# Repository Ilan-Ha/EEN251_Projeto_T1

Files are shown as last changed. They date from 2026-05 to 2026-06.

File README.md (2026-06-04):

# Bebedouro Inteligente para Pets

## Integrantes do Grupo:
- Diego Mourão Oliveira
- Ilan Hameiry
- Luca Lopes Martinho

## Descrição do Projeto

O projeto consiste no desenvolvimento de um dispositivo IoT voltado para o fornecimento de água corrente para animais de estimação (pets), com foco em uso residencial.

O objetivo principal é oferecer uma forma mais atrente e confortável de hidratação para o animal, simulando o fluxo de água corrente, além de monitorar a frequência com que o pet utiliza o bebedouro.

O sistema será ativado automaticamente apenas quando houver presença do animal próxima ao dispositivo, evitando desperdício de energia e água.

## Funcionamento do Sistema

O bebedouro funcionará em ciclo contínuo de circulação de água entre a bomba e o reservatório, simulando água corrente.

Por meio de um sensor de presença por distância (ultrassônico), o sistema será ativado automaticamente quando o animal se aproximar.

Após a detecção, o dispositivo permanecerá ligado por alguns segundos mesmo após a ausência de presença, garantindo tempo suficiente para o pet se hidratar.

Além disso, o sistema contará com:

- Iluminação interna por LEDs, acionada automaticamente quando a luminosidade do ambiente estiver baixa;
- Display informativo com dados importantes de uso;
- Monitoramento do nível de água no reservatório;
- Alertas de nível baixo de água;
- Botão de ativação manual;
- Botão de reset do sistema;
- Envio de notificações e informações para um software externo via Bluetooth.

## Objetivos do Projeto

- Melhorar a experiência de hidrtação dos pets;
- Automatizar o fornecimento de água;
- Reduzir desperdícios de energia e água;
- Permitir o monitoramento do uso do bebedouro;
- Fornecer alertas e informações em tempo real ao usuário.

## Requisitos do Sistema

### Requisitos Obrigatórios

| ID | Requisito | Tipo |
|---|---|---|
| RO-01 | Água circulando entre bomba e funil | Obrigatório |
| RO-02 | Detector de presença por distância (sensor ultrassônico) | Obrigatório |
| RO-03 | Iluminação em LED quando necessário | Obrigatório |
| RO-04 | Botão para ativação manual | Obrigatório |
| RO-05 | Botão de reset | Obrigatório |

### Requisitos Desejáveis

| ID | Requisito | Tipo |
|---|---|---|
| RD-01 | Display com informações úteis de uso: nível de água e número de ativações | Desejável |
| RD-02 | Mensagem via Bluetooth quando houver presença detectada ou nível baixo de água | Desejável |
| RD-03 | Sensor de nível de água | Desejável |

### Requisitos Opcionais

| ID | Requisito | Tipo |
|---|---|---|
| ROP-03 | Programação de ativação em intervalos de tempo definidos | Opcional |

## Diagrama de Blocos
```mermaid
flowchart TD
    MCU["Microcontrolador<br/>(Raspberry Pi Pico)"]

    OLED["Display<br/>OLED I2C<br/>128x32 Px"]
    RTC["Módulo Real Time Clock<br/>DS1307 (Opcional)"]
    LDR["Sensor de Luz<br/>LDR"]
    SOIL["Sensor de nível<br/>de água"]
    BT["Módulo Bluetooth<br/>HM10"]

    LEVEL1["Conversor de Nível Lógico<br/>(5V ↔ 3.3V)"]
    US["Sensor de Distância<br/>Ultrassom HC-SR04"]

    LEVEL2["Conversor de Nível Lógico<br/>(5V ↔ 3.3V)"]
    RELAY["Módulo Relé"]
    PUMP["Mini Bomba de Água<br/>DC-JT160"]

    MCU --> OLED 
    RTC --> MCU
    LDR --> MCU
    SOIL --> MCU
    MCU --> BT

    US --> LEVEL1
    LEVEL1 --> MCU

    MCU --> LEVEL2
    LEVEL2 --> RELAY
    RELAY --> PUMP

    %% Optional styling
    classDef sensor fill:#cfe8f3,stroke:#333,stroke-width:1px;
    classDef converter fill:#f4c542,stroke:#333,stroke-width:1px;
    classDef relay fill:#6abf4b,stroke:#333,stroke-width:1px;
    classDef controller fill:#cfe8f3,stroke:#333,stroke-width:2px;

    class MCU controller;
    class OLED,RTC,LDR,SOIL,BT,US,PUMP sensor;
    class LEVEL1,LEVEL2 converter;
    class RELAY relay;
    classDef default fill:#cfe8f3,color:#000,stroke:#000,stroke-width:2px;

    linkStyle default stroke:#000,stroke-width:2px;
```

## Softwares Utilizados

Durante o desenvolvimento do projeto foram utilizados os seguintes softwares:

- KiCad — utilizado para esquematização eletrônica e desenvolvimento do diagrama/layout da PCB;
- Thonny — utilizado para programação, testes e depuração do Raspberry Pi Pico;
- Autodesk Fusion 360, Solidworks — utilizados para modelagem 3D da estrutura do bebedouro;

## Tecnologias Envolvidas

O projeto utiliza conceitos de:

- Internet das Coisas (IoT)
- Sensores ultrassônicos
- Sensores de nível de água
- Iluminação automatizada com LEDs
- Comunicação via Bluetooth
- Sistemas embarcados
- Automação residencial

## Imagens do Modelo

| Vista Frontal | Vista Lateral |
| :---: | :---: |
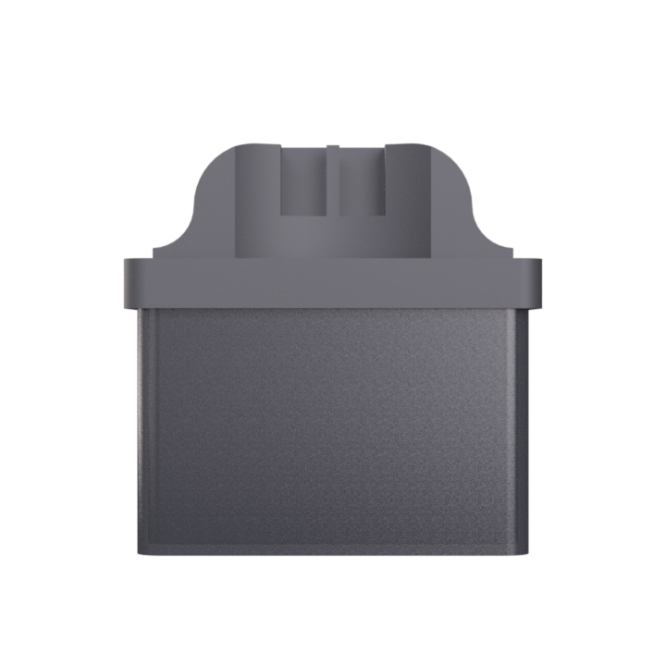
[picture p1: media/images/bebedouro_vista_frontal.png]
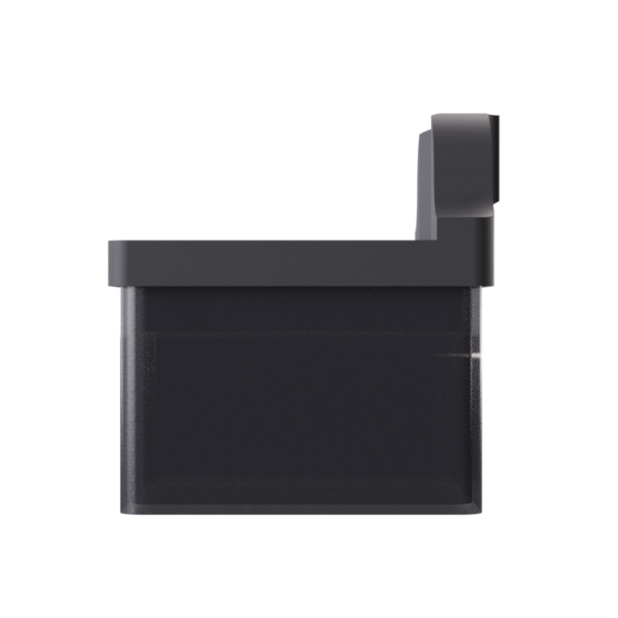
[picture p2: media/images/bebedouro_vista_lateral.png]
|  |  |
| Vista Superior | Vista Isométrica |
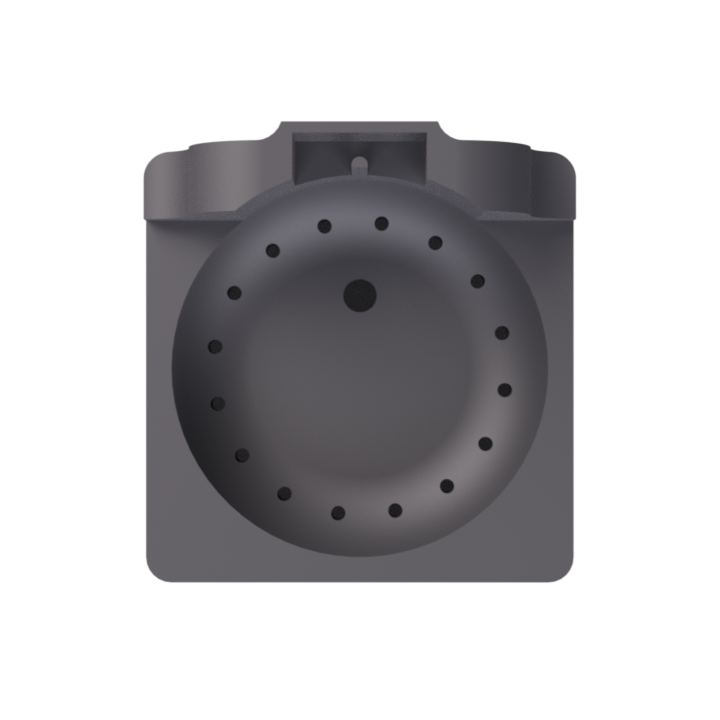
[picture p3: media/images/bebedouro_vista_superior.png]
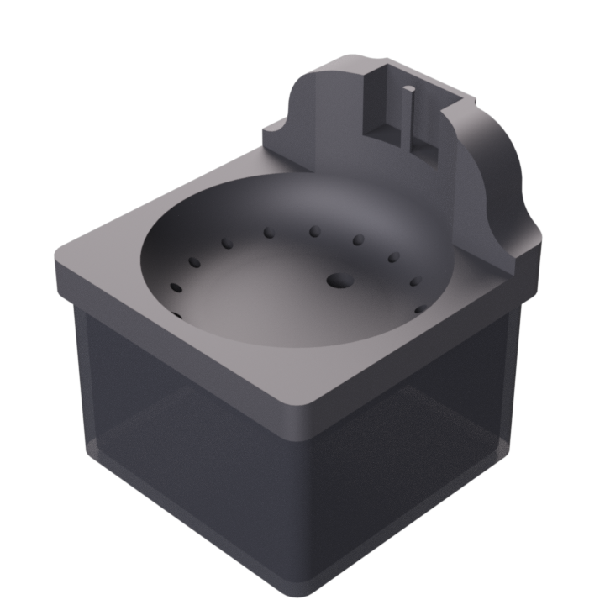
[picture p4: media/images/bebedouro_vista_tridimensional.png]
|  |  |

## Apresentação do Projeto em Vídeo

Confira o funcionamento e a apresentação completa do Bebedouro Inteligente no vídeo abaixo:

[Clique aqui para assistir ao vídeo](https://youtu.be/lJpa5DYjjUw)

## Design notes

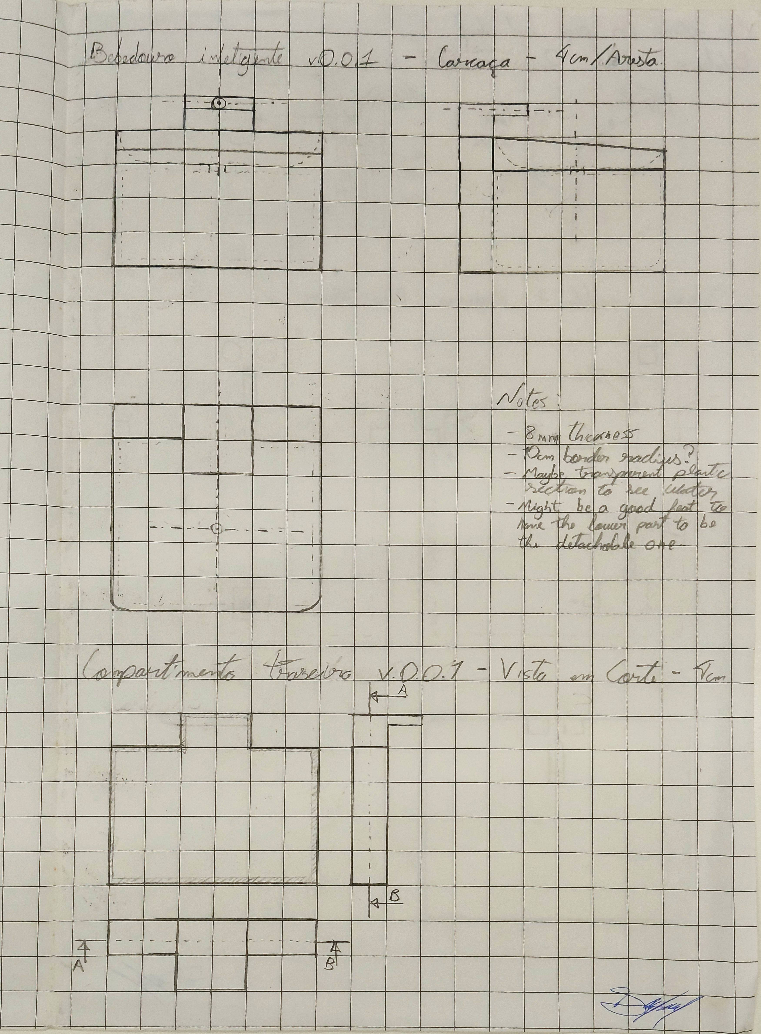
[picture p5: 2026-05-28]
media/3d_case_concept_v1.jpg

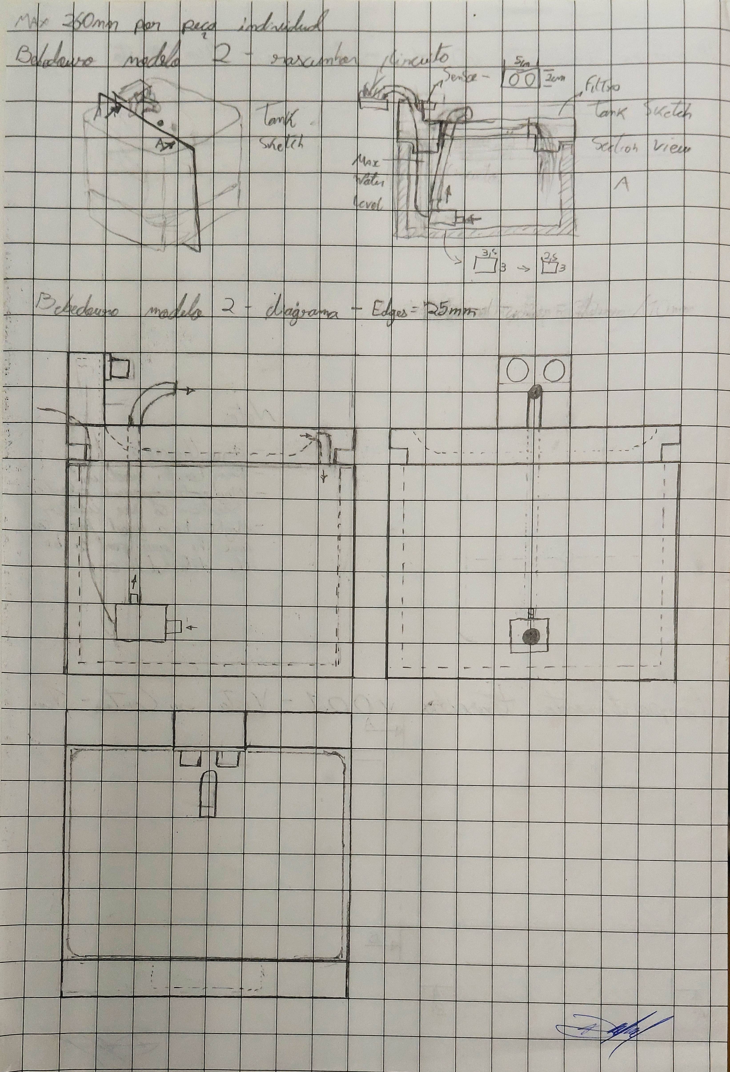
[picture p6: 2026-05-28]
media/3d_case_concept_v2.jpg

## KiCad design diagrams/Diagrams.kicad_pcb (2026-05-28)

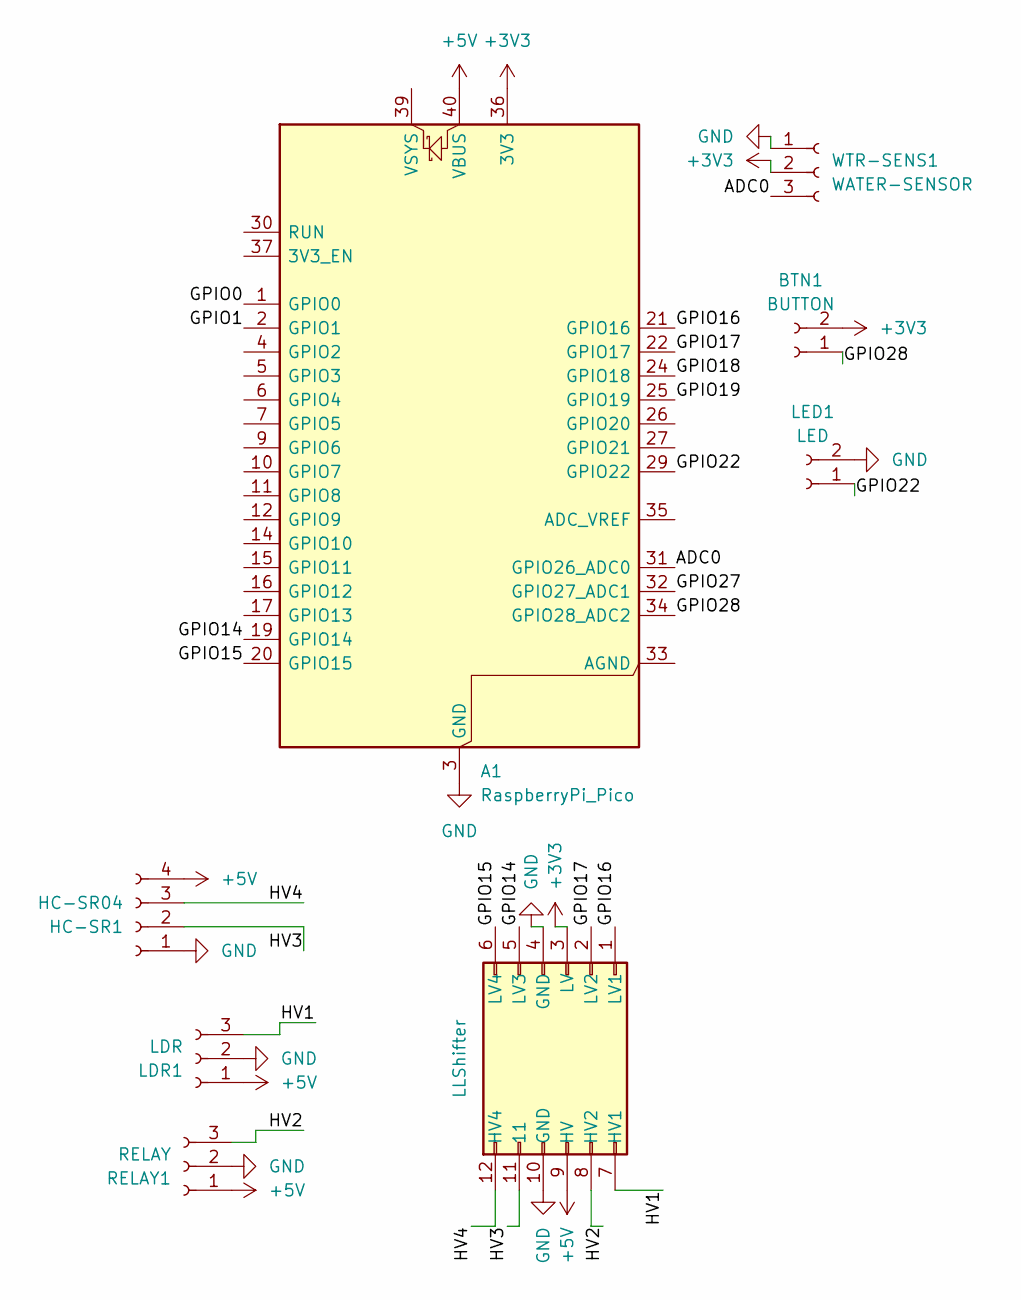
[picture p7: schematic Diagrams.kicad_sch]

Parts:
A1: RaspberryPi_Pico; RaspberryPi_Pico_Common_Unspecified
BTN1: BUTTON; SolderWire-0.25sqmm_1x02_P4.2mm_D0.65mm_OD1.7mm
HC-SR1: HC-SR04; SolderWire-0.25sqmm_1x04_P4.2mm_D0.65mm_OD1.7mm
LDR1: LDR; SolderWire-0.25sqmm_1x03_P4.2mm_D0.65mm_OD1.7mm
LED1: LED; SolderWire-0.25sqmm_1x02_P4.2mm_D0.65mm_OD1.7mm
LSA1: LLShifter; LLShifer-Footprint
RELAY1: RELAY; SolderWire-0.25sqmm_1x03_P4.2mm_D0.65mm_OD1.7mm
WTR-SENS1: WATER-SENSOR; SolderWire-0.25sqmm_1x03_P4.2mm_D0.65mm_OD1.7mm

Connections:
+3V3: A1.36 (3V3), BTN1.2 (IN), LSA1.3 (LV), WTR-SENS1.2 (VCC)
+5V: A1.40 (VBUS), HC-SR1.4 (VCC), LDR1.1 (VCC), LSA1.9 (HV), RELAY1.1 (VCC)
/ADC0: A1.31 (GPIO26_ADC0), WTR-SENS1.3 (SIGNAL)
/GPIO0: A1.1 (GPIO0)
/GPIO1: A1.2 (GPIO1)
/GPIO14: A1.19 (GPIO14), LSA1.5 (LV3)
/GPIO15: A1.20 (GPIO15), LSA1.6 (LV4)
/GPIO16: A1.21 (GPIO16), LSA1.1 (LV1)
/GPIO17: A1.22 (GPIO17), LSA1.2 (LV2)
/GPIO18: A1.24 (GPIO18)
/GPIO19: A1.25 (GPIO19)
/GPIO22: A1.29 (GPIO22), LED1.1 (GND)
/GPIO27: A1.32 (GPIO27_ADC1)
/GPIO28: A1.34 (GPIO28_ADC2), BTN1.1 (VCC)
/HV1: LDR1.3 (DO), LSA1.7 (HV1)
/HV2: LSA1.8 (HV2), RELAY1.3 (IN)
/HV3: HC-SR1.2 (ECHO), LSA1.11
/HV4: HC-SR1.3 (TRIG), LSA1.12 (HV4)
GND: A1.3 (GND), A1.8 (GND), A1.13 (GND), A1.18 (GND), A1.23 (GND), A1.28 (GND), A1.38 (GND), HC-SR1.1 (GND), LDR1.2 (GND), LED1.2 (VCC), LSA1.4 (GND), LSA1.10 (GND), RELAY1.2 (GND), WTR-SENS1.1 (GND)

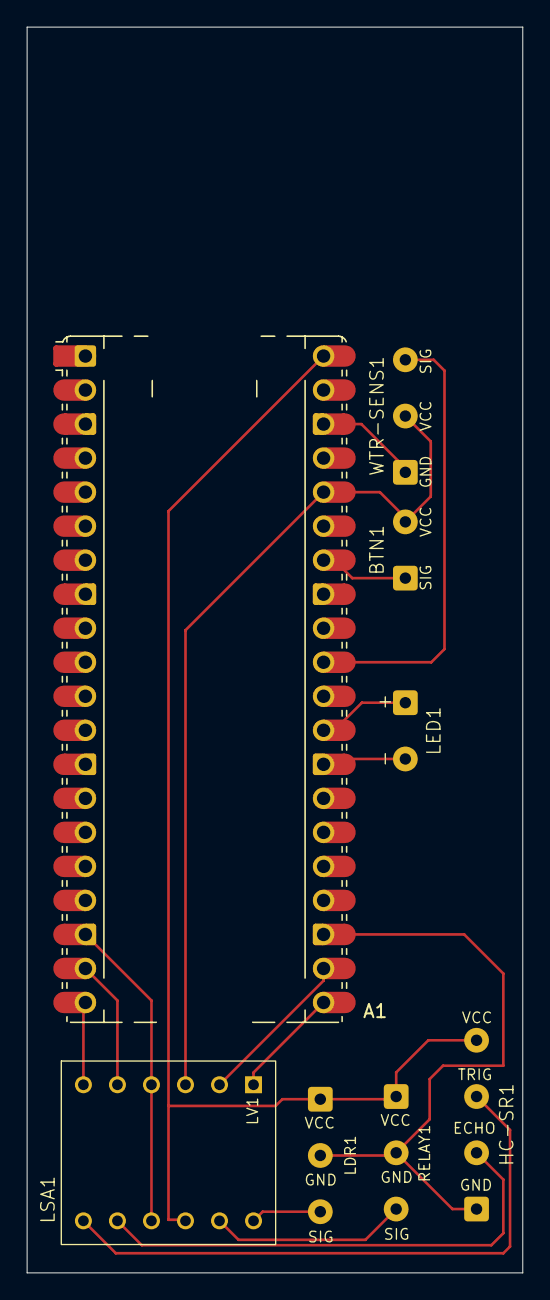
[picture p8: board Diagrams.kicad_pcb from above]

Board: 2 copper layers, 37.0 x 93.0 mm, 8 parts (0 on the bottom side), 14 nets.

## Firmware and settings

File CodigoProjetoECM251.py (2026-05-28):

from machine import Pin, time_pulse_us, ADC
from utime import sleep_us, sleep

relay = Pin(17, Pin.OUT)
trigger = Pin(15, Pin.OUT)
echo = Pin(14, Pin.IN)
ldr = Pin(16, Pin.IN)
led = Pin(22, Pin.OUT)
button = Pin(28, Pin.IN, Pin.PULL_DOWN)
water_pin = Pin(27, Pin.OUT)
water_sensor = ADC(26)
led_debbug = Pin(25,Pin.OUT)

buttonOn = False
led_debbug.value(0)

DELAY_RELAY_ON = 3

DELAY_RELAY_OFF = 0

def ldr_led_interrupt(pin):
    if ldr.value():
        led.value(1)
        #print(f"ligou: {ldr.value()}")
    else:
        led.value(0)
        #print(f"desligou: {ldr.value()}")
      
def send_pulse_and_wait():
        """
        Send the pulse to trigger and listen on echo pin.
        We use the method `machine.time_pulse_us()` to get the microseconds until the echo is received.
        """
        trigger.value(0) # Stabilize the sensor
        sleep_us(5)
        trigger.value(1)
        # Send a 10us pulse.
        sleep_us(10)
        trigger.value(0)
        try:
            pulse_time = time_pulse_us(echo, 1, 30000)
            # time_pulse_us returns -2 if there was timeout waiting for condition; and -1 if there was timeout during the main measurement. It DOES NOT raise an exception
            # ...as of MicroPython 1.17: http://docs.micropython.org/en/v1.17/library/machine.html#machine.time_pulse_us
            if pulse_time < 0:
                MAX_RANGE_IN_CM = 500 # it's really ~400 but I've read people say they see it working up to ~460
                pulse_time = int(MAX_RANGE_IN_CM * 29.1) # 1cm each 29.1us
            return pulse_time
        except OSError as ex:
            if ex.args[0] == 110: # 110 = ETIMEDOUT
                raise OSError('Out of range')
            raise ex

def distance_mm():
        """
        Get the distance in milimeters without floating point operations.
        """
        pulse_time = send_pulse_and_wait()

        # To calculate the distance we get the pulse_time and divide it by 2 
        # (the pulse walk the distance twice) and by 29.1 becasue
        # the sound speed on air (343.2 m/s), that It's equivalent to
        # 0.34320 mm/us that is 1mm each 2.91us
        # pulse_time // 2 // 2.91 -> pulse_time // 5.82 -> pulse_time * 100 // 582 
        mm = pulse_time * 100 // 582
        return mm
    
def turn_relay_on():
    relay.value(1)
    sleep(DELAY_RELAY_ON)
    #print(f"rele ligado: {relay.value()}")
def turn_relay_off():
    relay.value(0)
    sleep(DELAY_RELAY_OFF)
    #print(f"rele desligado: {relay.value()}")
    
def is_button_pressed():
    #print(f"botao: {button.value()}")
    return button.value() == 1
    
def control_pump(target_distance_in_mm):
    #print("botao: ",buttonOn)
    if buttonOn:
        turn_relay_on()
        #print("ligou")
    elif distance_mm() <= target_distance_in_mm:
        turn_relay_on()
        #print("ligou")
    else:
        turn_relay_off()
        #print("desligou")
        
def button_handler(pin):
    global buttonOn
    buttonOn = not buttonOn
    
    if(buttonOn):
        led_debbug.value(1)
    else:
        led_debbug.value(0)

ldr.irq(trigger=Pin.IRQ_FALLING, handler=ldr_led_interrupt)
button.irq(trigger=Pin.IRQ_RISING, handler=button_handler)

while True:
    control_pump(110)
    value = water_sensor.read_u16()
    
    # Optional: Convert to percentage
    percentage = (value / 65535) * 100
    
    #print("Water Level Reading:", percentage)
    
    if(percentage > 15):
        water_pin.value(1)
    else:
        water_pin.value(0)

    
    

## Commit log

2026-04-19 feat: adiciona controle automático de relé com sensor ultrassônico e controle de led com sensor LDR
    - Sensor ultrassônico HC-SR04 para medição de distância em mm
    - Relé para posterior acionamento automático da bomba d’água
    - Sensor LDR para controle de iluminação com LED
    Funcionalidades adicionadas:
    - Envio de pulso e leitura de resposta do sensor ultrassônico
    - Cálculo da distância em milímetros sem uso de ponto flutuante
    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
2026-04-19 Adiciona delay no controle do relé da bomba
    Foi adicionado um tempo de espera no acionamento e desligamento do relé da bomba utilizando sleep(), com as variáveis DELAY_RELAY_ON e DELAY_RELAY_OFF.
    Essa alteração evita que o relé desligue imediatamente quando o sensor ultrassônico deixa de detectar presença.
2026-04-19 Adiciona controle manual por botão e refatora lógica da bomba
    Foi implementado um botão para acionamento manual da bomba, permitindo ligar o relé independentemente da leitura do sensor ultrassônico.
    A antiga função control_pump_by_distance_mm() foi substituída por control_pump(), unificando a lógica de controle em uma única função. Agora, o botão manual possui prioridade sobre o modo automático,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
    Também foi adicionada a configuração Pin.PULL_DOWN no botão para evitar leituras instáveis no pino de entrada.
2026-04-22 feat: adiciona deteccao de nivel de agua
2026-04-29 feat: adiciona pasta media com vídeos de testes do protótipo
    - adiciona vídeo demonstrando a detecção de movimento pelo sensor ultrassônico
    - adiciona vídeo demonstrando a detecção de baixa iluminação para acionamento dos LEDs
    - organiza arquivos de mídia para documentação e apresentação do projeto
2026-05-23 Adiciona diagramas do projeto feitos em KiCad
    [Diagrams.kicad_pcb, Diagrams.kicad_sch]
2026-05-23 feat(lib): adiciona biblioteca de footprints do KiCad
2026-05-24 update: mudança nos pinos led e button
2026-05-24 update: diagramas
    - alterações pequenas no diagrama esquemático
    - diagrama pcb inicial implementado
    [Diagrams.kicad_pcb, Diagrams.kicad_sch]
2026-05-27 update: novo esquemático
    - Esquemático refeito
    - Nova biblioteca adicionada
    [Diagrams.kicad_sch]
2026-05-27 udpate: mais algumas mudanças
    [Diagrams.kicad_sch]
2026-05-27 update: atribuição de footprints básicas na schematic
    [Diagrams.kicad_pcb, Diagrams.kicad_sch]
2026-05-27 update: altera botao e led onboard
    - Muda o comportamento do botão, anteriormente de segurar, para alternar.
    - Adição de led de debug ao pressionar o botão.
2026-05-28 feat(pcb): finalizar layout da PCB pronto para impressão
    - concluir roteamento da placa
    - ajustar posicionamento dos módulos
    - corrigir outline da PCB em Edge.Cuts
    - prontificar PCB para fabricação/impressão
    [Diagrams.kicad_pcb, Diagrams.kicad_sch]
2026-05-28 refactor: atualizar mapeamento de GPIOs para corresponder ao da PCB
    - alterar pinos utilizados pelos módulos ldr, led, button, trigger, echo e relay no arquivo .py conforme organização física da placa
    - manter compatibilidade com o layout final para impressão
2026-05-28 Atualiza README com membros do grupo de detalhes dos softwares usados
2026-06-03 docs: adiciona bebedouro.stl
    [bebedouro.stl]
2026-06-03 docs: adiciona modelo do bebedouro
    [bebedouro_v3_montado.STL]
2026-06-03 feat: adiciona modelo do bebedouro
    [modelo_bebedouro.stl]
2026-06-03 Update(README): adiciona diagrama de blocos
2026-06-03 refactor: modifica foto de vista superior
